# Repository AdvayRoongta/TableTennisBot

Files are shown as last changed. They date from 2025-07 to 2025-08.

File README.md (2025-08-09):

# Table Tennis Robot

<h2>This is a 1-axis robot that will play table tennis with me when no one else will.</h2>



<br>
This uses a vslot with a gantry plate on top. Connected to the gantry are my camera and paddle. The gantry will move based on camera input to the motor, which is connected to the gantry via a belt. The goal is to move along one axis to return the ball. The camera uses a simple contour recognition to find the ball and uses the ball's coordinates to see if it in the mid, left or right of the view. (TableTennisBot and TableTennisRobot are interchangable)

# It has:
<h3>An ESP32-S3-EYE Microcontroller and Camera, along with a matching mount.</h3>



<h3>2 twin table attachements</h3>



<h3>A Paddle mount </h3>



<h3>A Idler Mount</h3>



<h3>A Motor mount</h3>


<h3>Here is the wiring for the motor:</h3>


# Why

Most Table Tennis robots are developed at Google Deepmind or MIT. Although they are way better than mine, they cost thousands of dollars to make and develop. I made mine to just return the ball to a simple practice shot, rather than all different possible shots. I also really like playing table tennis and there is not always someone to play with me. Practicing by myself is really hard since my garage is cluttered and the balls get lost easily.

<h1>Notes</h1>:
I have put my full assembly step file in both the production folder and outside of the folder for ease of access

# BOM (Scroll all the way down)

| Vendor | Name | Price  | Description | Notes | Link | |
|---|---|---|---|---|---|---|
| VXB | V-Slot 20 x 20mm | $38.28 | Vslot, 1500mm | | https://vxb.com/products/20mm-linear-rail-5-feet-length-tubing-2020-aluminu?variant=43583118115051 | |
| | | | | | | |
| | | | | | | |
| Biqu | Timing Belt | $4.85  | All Biqu products bought together | | https://biqu.equipment/products/hot-sale-10meter-gt2-6mm-open-timing-belt-width-6mm-gt2-belt-for-3d-printer-parts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 | |
| Biqu | Idler x2 | $5.04  | All Biqu products bought together | | https://biqu.equipment/products/3d-printer-parts-16-teeth-synchronous-wheel-pulley-wheel-driven-wheel-perlin-16-2gt-toothed-gear-bore-3mm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 | |
| Biqu | Shipping+Tax | $6.58  | All Biqu products bought together | | | |
| | | | | | | |
| Aliexpress | M5 Screws | $2.27  | Aliexpress items bought together | | https://www.aliexpress.us/item/3256805692722422.html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 | |
| Aliexpress | M5 Tnuts | $1.52  | | | https://www.aliexpress.us/item/3256805435856022.html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 | |
| Aliexpress | Motor | $6.19  | Nema 17 | | https://www.aliexpress.us/item/2255800222409012.html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 | |
| Aliexpress | TMC2209 | $2.38  | Motor Driver | | https://www.aliexpress.us/item/3256805074646808.html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 | |
| Aliexpress | 2020 V-slot Wheels Gantry Plate | $6.28  | Gantry Plate + Wheels | | https://www.aliexpress.us/item/3256808485831638.html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 | |
| aliexpress | VHB | $3.29  | VHB Tape like @LoganPeterson said | | https://www.aliexpress.us/item/3256807144002696.html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 | |
| aliexpress | Shipping+Tax | $2.00  | All Aliexpress items bought together | | | |
| | | | | | | |
| | | | | | | |
| Total | | $78.68 | | | | |

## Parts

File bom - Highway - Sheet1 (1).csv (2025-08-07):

Vendor | Name | Price | Description | Notes | Link
VXB | V-Slot 20 x 20mm | $38.28 | Vslot, 1500mm | I know $38.28 is alot, so I have permission from acon. https://hackclub.slack.com/archives/C08Q1H6D79B/p1749947689245759?thread_ts=1749512474.276809&cid=C08Q1H6D79B |  | https://vxb.com/products/20mm-linear-rail-5-feet-length-tubing-2020-aluminu?variant=43583118115051
Biqu | Timing Belt | $4.85 | All Biqu products bought together |  | https://biqu.equipment/products/hot-sale-10meter-gt2-6mm-open-timing-belt-width-6mm-gt2-belt-for-3d-printer-parts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
Biqu | Idler x2 | $5.04 | All Biqu products bought together |  | https://biqu.equipment/products/3d-printer-parts-16-teeth-synchronous-wheel-pulley-wheel-driven-wheel-perlin-16-2gt-toothed-gear-bore-3mm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
Biqu | Shipping+Tax | $6.58 | All Biqu products bought together
Aliexpress | M5 Screws | $2.27 | Aliexpress items bought together |  | https://www.aliexpress.us/item/3256805692722422.html?mp=1
Aliexpress | M5 Tnuts | $1.52 |  |  | https://www.aliexpress.us/item/3256805435856022.html?mp=1
Aliexpress | Motor | $6.19 | Nema 17 |  | https://www.aliexpress.us/item/2255800222409012.html?mp=1
Aliexpress | TMC2209 | $2.38 | Motor Driver |  | https://www.aliexpress.us/item/3256805074646808.html?mp=1
Aliexpress | 2020 V-slot Wheels Gantry Plate | $6.28 | Gantry Plate + Wheels |  | https://www.aliexpress.us/item/3256808485831638.html?sourceType=1
aliexpress | VHB | $3.29 | VHB Tape like @LoganPeterson said |  | https://www.aliexpress.us/item/3256807144002696.html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
aliexpress | Shipping+Tax | $2.00 | All Aliexpress items bought together
Total |  | $78.68

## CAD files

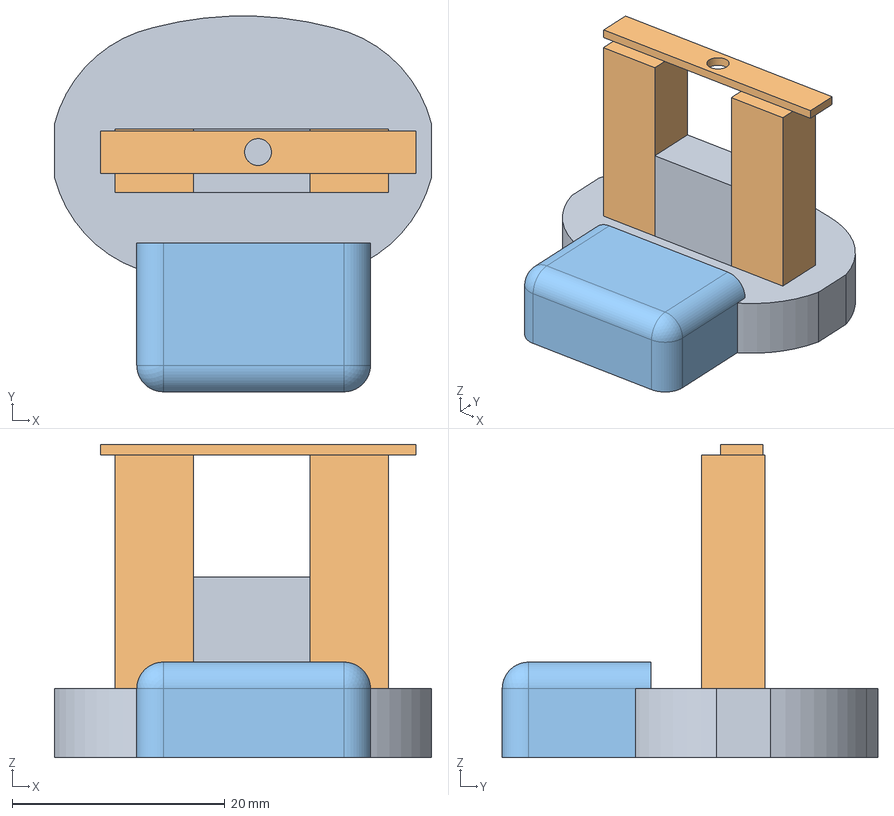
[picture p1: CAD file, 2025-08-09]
Production (CAD)/paddleattachement v9.step
35.5 x 35.4 x 29.5 mm

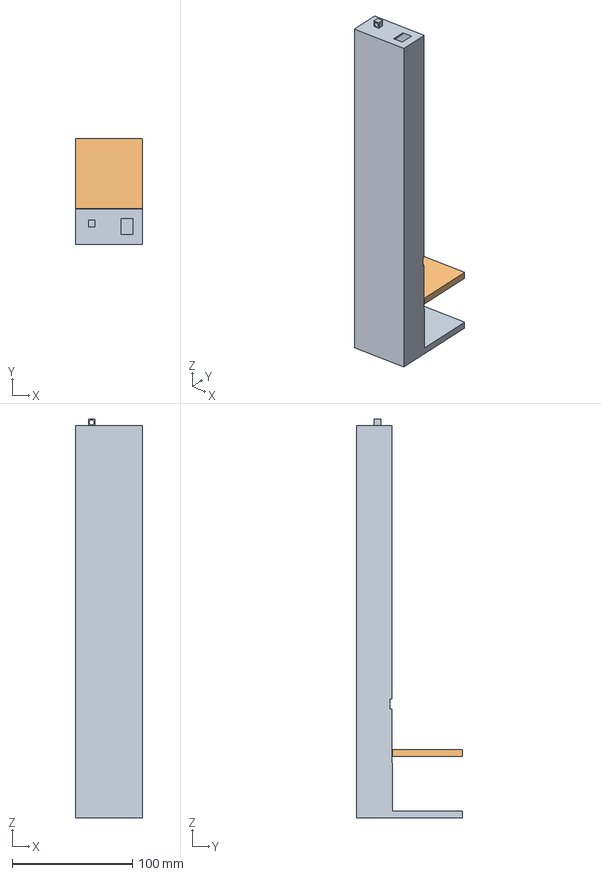
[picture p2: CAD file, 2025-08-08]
Production (CAD)/Table_attachement real v1.step
55.7 x 87.6 x 331.3 mm

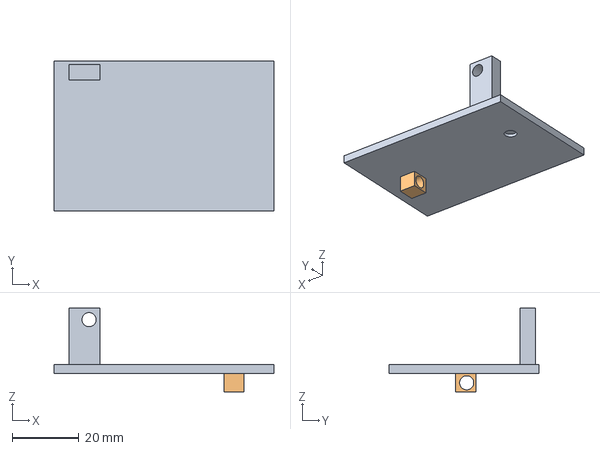
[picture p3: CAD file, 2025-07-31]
Production (CAD)/TABLE_MOTOR_CONNECTOR.step
66.0 x 45.0 x 25.2 mm

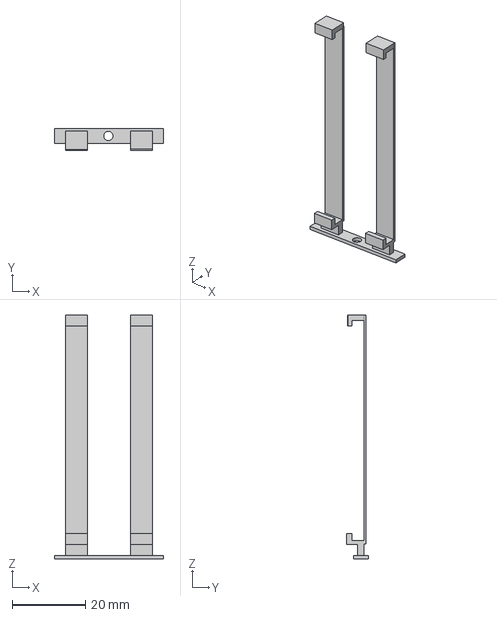
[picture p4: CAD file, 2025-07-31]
Production (CAD)/mcu_mount.step
29.7 x 5.93 x 66.7 mm

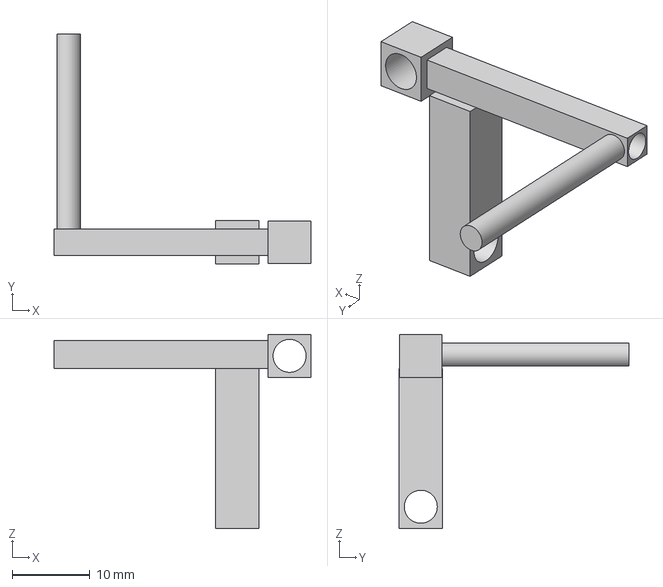
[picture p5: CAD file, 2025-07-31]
Production (CAD)/Idler_mount.step
33.0 x 29.5 x 24.9 mm

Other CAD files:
Production (CAD)/theREALmotormount.step

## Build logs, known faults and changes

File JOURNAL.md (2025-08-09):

---
title: "TABLE TENIS ROBOT"
author: "Advay Roongta"
description: "Robot that moves paddle along 1 axis to return table tennis ball"
created_at: "June 7 2025"
time_spent: "21.5 Hours"
---

# Note:
I haven't been working on this every single day, so for example the gap between July 21 and 23, I didn't do anything on this during the 22nd.

# June 9th: Just researching and finalized a rough design, 2hrs

[So heres what I figured out so far about how it will work:
Nema stepper motor with a keyed belt attachement for the timing belt. The motor will be stationary and the belt will go around the vslot with an idler (wheel) on the other side. Then theres gonna be a gantry (plate) with wheels that gets attched to the belt just by feeding it through the holes on the side and securing it with tape or bands. For ball tracking perhaps an ESP-EYE from Visioneer that goes on top of the gantry plate. Then it could work by recognizing the ball by color and making sure it is in a certain range of x values that will be in the middle, and if the ball is not in that ideal range it will move depending on how out of the range it is.
The stuff I would have to do:<br>
Firmware
CAD: [
Mount for paddle to gantry<br>
Mounts for table to v-slot<br>
Mount for gantry to mcu<br>
Mount for motor to vslot and idler
]

Timing Belt

Idler Pulley Plate

V-Slot NEMA 17 Linear Actuator

**Total time spent: 2h**

# June 10th: Started code, time spent: 1hr
Its in python and so I just wrote the framework with OPenCV. Its only 20ish lines right now. Since i'm using the HoughCirlces function from OpenCV I had to meausure the minimun and maximun pixel radius of a table tennis ball. I took webcam photos from 7 ft and 1 ft away and measured it using this website called ImageJS.
<br>


# June 13th: Implemented color trakcing with code,2.5hr
I made the ball only register if it was white in color, and this works a lot better, and cuts out most other noise. Before it would think that my fingers and nose and eyes were circles. I also messed around with the Hough transform parameters to give me the best results. It works much better at close and moderate distances, but not so much at farther distances. I am exploring other options such as an elliptical transform. I also wrote some code that only chooses the ball if it is moving from its current position, but the color tracking kind of makes that redundant since in the real case (me playing ping pong) there will only be 1 white ball. <br>
 
<br>
# June 15th: Ball tracking complete with mask, 2hr:
Since the hough transform wasnt working well for farther distances, I used a color mask to first filter out all colors except orange (which will now be the color of the ball). Then it locates the ball based on the contours and size, and finds the center by using a cv2 function that returns the center coords for the smallest cirlce that fits around the contour. TLDR; It works! ONTO THE CAD PROBABLY NOW<br>

<br>

# June 30: I'm ill
I've been traveling for the past 2 weeks and fell quite sick a few days ago.
<br>
# July 21: Motor mount done, 4 hours (first CAD)
I made a mount from the vslot to the motor by using a threaded tnut that goes inside of the vslot extrusion, and then a screw that goes in there. The mount has a threaded hole for the screw, and a larger one for the motor, connected the two. I ran into a few issues about parts not working together such as the first few tnuts I found being too big. Through this proccess I also did a little bit of part sourcing, like finding the exact vslot I will buy when I get the grant :).
<br>

<br>

<br>


<br>

# July 23: Fixed motor mount, added table mount: 3.5 hrs

So I first realized my motor mount was a bit flawed because it was only connected to the vslot at one point, which it not too stable, so I added another tnut and screw at the bottom. This fixed the issue, but then a few hours later I realized that having it at the bottom would block the belt from going around the vslot, which is vital, so I had to move it to the side. I also realized that the motor was quite high up, so I just lowered it down to make it centered with the vslot. I also today made the table mount to connect the whole thing to the table. I attached it to one side by using the same bottom platform for the motor, I just made a extrusion downwards and then a screw hole, there is also a screw hole on the top of the mount so they can connect with a screw. Tmrw I will do the idler mount and attach the other table mount. 






# July 24: Added Idler mount, 1hr

Today I added the idler mount to the other side of the vslot. It works the same way as the motor mount, except it attaches to the idler by going inside it (since it has a hole) rather than around the circumfrence. Didn't do much today but yeah.



# July 25: Attached other table mount, 1hr
So today I first attached the other table mount to the other side of the vslot where the idler is. I just made an extrusion down from my idler attachemetn and put a screw hole that can be conncted via a screw to the screw hole on the mount. this is the same way the other one works. I had to dimension the whole thing in a drawing to make sure that the two table mounts were lined up, and uh yeah. The nice thing about my table mount design is that because it uses screws, depending on the length of the screws, the mounts can be moved in parrallel to the table, meaning that no matter what happens, they will be able to fit on the table as long as they are the same height. This is because if the whole vslot system is 4.9 ft but the table is 5ft I can just move the mounts farther towards the screw head (if its facing away from the table) and the vslot system will get longer.




# July 27: MCU Mount, 1.5 hr

So today I made the mount for my mcu (which has a camera) to the grantry plate I chose. Because I have the mcu already at my house I was able to measure everything and make a simple but working mount that attaches onto the sides. The reason it wont go in the middle is because I dont want to obstuct the Micro USB Port and because the chip on the back of the board bumps out, and I didnt want to waste the fillament. This is sturdy enough by keeping the board straight and attachning from both sides. The reason I didnt make it go around the front of the board more is because it would then block the ports that I will need to connect to my motor. Also, in the gantry plate that i'm going to buy, the holes o the sides are big enough to fit the timing belt. I'm making good progress currently, the only part left to do is the paddle mount, which I think can be done in 1 day of locking in. 



<br>


# July 29, Paddle Mount+ Full assembly, 2hrs

OMFG I AM DONE. Today I worked on my paddle mount and did the complete CAD assembly. First I had to precisley measure my ping pong paddle's handle, which took way longer than it should have, because its not a normal oval or anything (as shown in the sketch picture) I also dont have callipers so I had to use a blue broken transperent half-ruler and constantly convert inches to mm. After that, because my paddle has a hole in it, I cadded a shaft in my mount to go inside the hole for additional grip. For attaching the mount to the gantry, I did it the same way I attached the mcu mount to the gantry, a plate with a screw hole. I had to make these twin bars connecting the plate with screw hole to the mount because they could not be directly jointed, due to the vslot being in the way. I made these bars pretty chunky because the paddle will wheigh a lot and it needs to be stable. For the complete assembly I just imported components and moved them in place. :)







# July 30, Firmware, 0.5hr

Just did the firmware and wiring to make the motor move. Today will be the day I also submit, I have now have to do parts sourcing and CAD renders. 



# 8/8, Color+Made paddle mount better.      0.5 hour

I added color to the project, and made the paddle mount have holders for pencils that I will connect to the paddle using VHB to make the connection stronger. I also made the mount thicker. 





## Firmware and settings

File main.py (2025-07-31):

import cv2 as cv
import numpy as np
import machine
import time

dir_pin = machine.Pin(2, machine.Pin.OUT)
step_pin = machine.Pin(3, machine.Pin.OUT)

def step_motor(direction, steps=10, delay=0.001):
    dir_pin.value(direction)
    for _ in range(steps):
        step_pin.value(1)
        time.sleep(delay)
        step_pin.value(0)
        time.sleep(delay)

camera = cv.VideoCapture(0)
camera.set(cv.CAP_PROP_FRAME_WIDTH, 640)
camera.set(cv.CAP_PROP_FRAME_HEIGHT, 480)

while True:
    success, frame = camera.read()
    if not success:
        break
    hsv = cv.cvtColor(frame, cv.COLOR_BGR2HSV)
  #white
    lower = np.array([10, 180, 180])
    upper = np.array([22, 255, 255])
  
    mask = cv.inRange(hsv, lower, upper)
    contours, _ = cv.findContours(mask, cv.RETR_EXTERNAL, cv.CHAIN_APPROX_SIMPLE)
    if contours:
        largest_contour = max(contours, key=cv.contourArea)
      
        if cv.contourArea(largest_contour) > 30:
            ((x, y), radius) = cv.minEnclosingCircle(largest_contour)
            M = cv.moments(largest_contour)
            if M["m00"] > 0:
                cx = int(M["m10"] / M["m00"])
                if cx < 270:
                    step_motor(0)
                elif cx > 370:
                    step_motor(1)
                center = (cx, int(M["m01"] / M["m00"]))
                cv.circle(frame, (int(x), int(y)), int(radius), (0, 255, 0), 2)
                cv.circle(frame, center, 5, (0, 0, 255), -1)
    cv.imshow("Ball Tracking", frame)
    cv.imshow("mask", frame)
    if cv.waitKey(1) & 0xFF == ord('q'):
        break

camera.release()
cv.destroyAllWindows()
